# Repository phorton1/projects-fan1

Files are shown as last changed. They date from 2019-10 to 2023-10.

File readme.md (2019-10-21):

## 3D PRINTED FAN with Brushless Motor

I live on a sailboat in the tropics.  A good working 12V fan is more than a luxury, it is a necessity.  They get used for 8, 12, or more hours per day, and apart from just the sheer wear and tear from so much use, they are also usually subject to high humidity and salty sea air.  I have 7 such fans on the boat (it's a big boat, with 3 cabins).   One in each of the guest cabins, two in the master cabin, two in the salon, and one over the stove that works as an exit fan to a nearby window. So, if the fans only last 6 months ... well, you can see that you will be replacing a lot of fans!

For over 10 years I have struggled to get a good working 12V fan at anything resembling a reasonable price.

Such fans for boats (and RVs) come in basically two genres:

* super cheap fans, that aren't even worth the effort
* expensive boutique fans that don't satisfy expectations

Basically you can get cheap fans with brushed motors and cheap steel or plastic housings, or expensive ones that don't seem to me to be worth the money. If you are interested in more details, here's a link to my "survey of existing fans" page: [Survey of Existing Fans](survey.md) where I cover mostly the "cons" of such fans.

But now that I have a 3d printer I was able to design **my own fan**, and I think it came out pretty good!

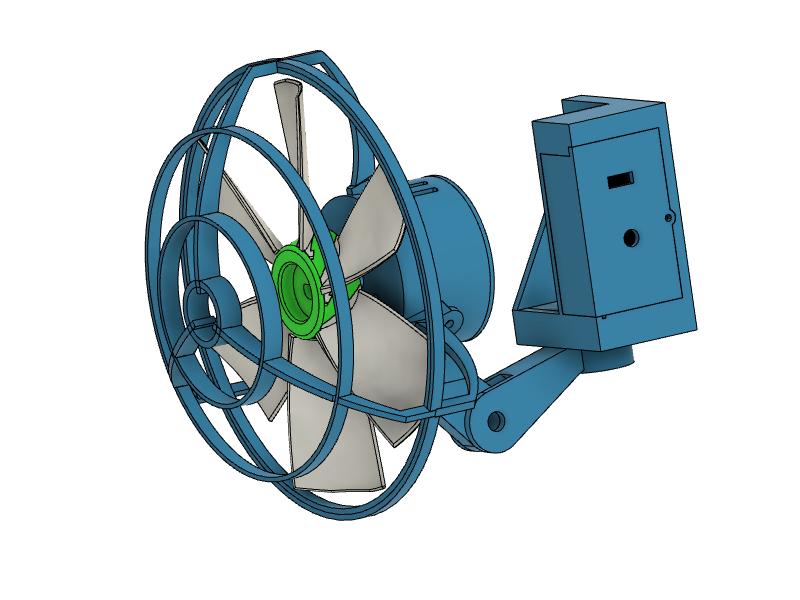
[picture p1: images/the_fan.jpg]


## MY SOLUTION

I went on ebay and bought a good brushless motor with dual ball bearings for $12.74.  To that I added a $3 arduino nano (which was really overkill for the project), a $1 rotary controller, a 50 cent switch, a little circuit board, and some wire, and designed and printed this fan.

The motor I chose was a Nidec 48F704K.   It seemed to have about the right specs for rpms and amperage at 12V.  They are actually a bit big for the fan I designed.  My fan has 180mm/7" blades and this motor could easily push 9" blades, but I wanted one that fit basically with the footprint of the "standard" fan I am replacing (which has 6" blades).

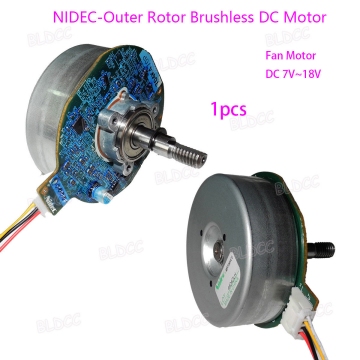
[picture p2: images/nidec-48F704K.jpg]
  **$12.74 on ebay**

**The motor takes short 3mm screws.**

I went through several design iterations, first on the fan blade, and then also on the shroud. Here's a pic of an early prototype.  Notice the bench power supply to the left, the laptop with fusion360 running and my Prusa 3d printer in the background.  With this setup I was able to test the fan at various voltages and to monitor and measure the current consumption:

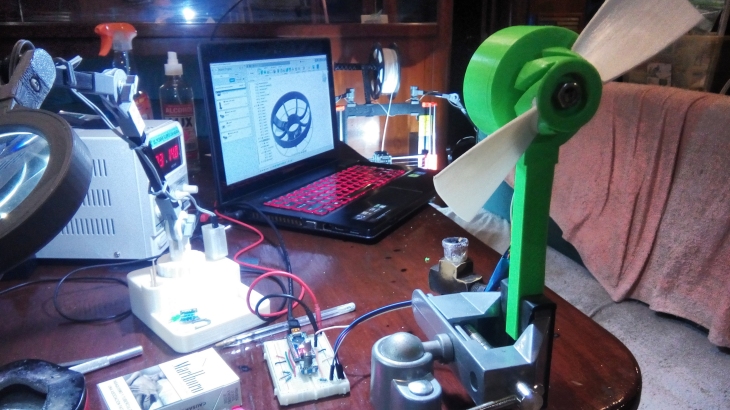
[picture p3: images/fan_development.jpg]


I was surprised at how much (negative) effect the shroud had on the performance.   I started with a heavy shroud that printed in one piece.  It took 11 hours to print, with supports!   That was for the birds!   I redesigned it  to be much thinner and less obtrusive to the airflow, and so that it could be printed in an hour or two, though it needs assembly. 

I had already (quickly) learned that it was better to print the blade itself in pieces and assemble it.   Printing it in one piece took a long time (like 8-10 hours), and (b) did not allow for replacing a single blade should one break.

Let me also add that this is **NOT THE FINAL effort** in this matter!  I have purchased more additional, and different types of brushless motors on Ebay and am looking forward to refining and generalizing the mounting etc.

## SLICING and PRINTING

All the STL files are in the [STL subdirectory](stl/).  I have provided the [Fusion 360 files](fusion/) as well.

I print almost everything at **0.30mm layer heights**, in "draft" quality on the Prusa, except the blades, which I printed at the Prusa 0.20mm "quality" setting.

I try to orient all the parts so that they are strongest in the required directions.  For the blade, to minimize the amount of supports, I print them on edge, as shown below:

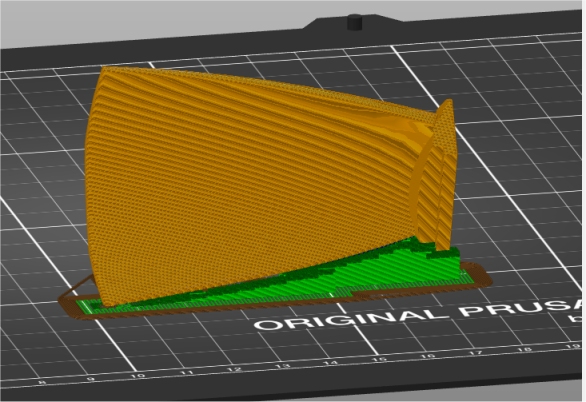
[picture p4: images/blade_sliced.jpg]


I print all the rings for the shroud in one go, with the slots facing upwards as shown below.

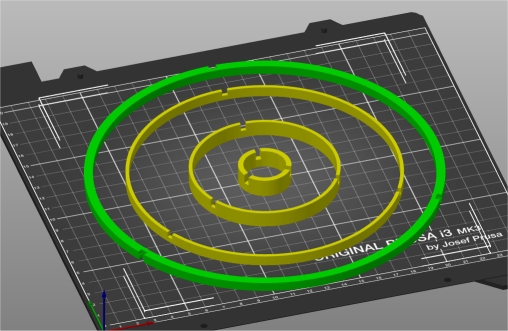
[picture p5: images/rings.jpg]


and the motor body, with supports, as shown below:

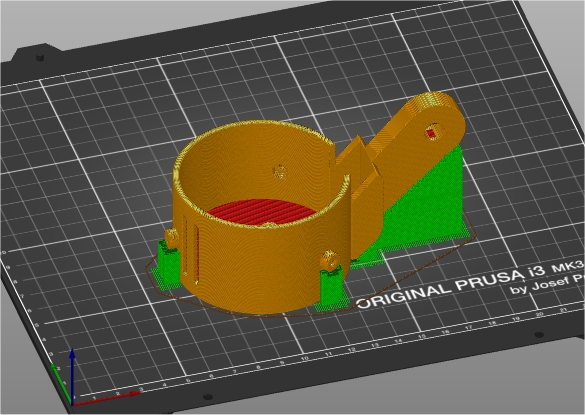
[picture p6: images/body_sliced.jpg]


The rest of the parts (bracket, struts, etc) are generally printed laying flat, or in whichever orientation makes the most sense.

## The Circuit

For the PWM motor control circuit, I simply used an Arduino Nano.  This was nice because I could hook it up directly to the boat's 12V system (which actually varies from about 12V upto 14.00V while charging) and it in turn could provide 5V that I could use with the rotary controller and for the PWM control signal to the motor.   Even so, it is overkill, so future designs will probably be based on the AT-TINY13 8 pin MPU with a dedicated 12V regulator, which sounds complicated but is actually less expensive ($1 vs $3) compared to the arduino and physically much smaller.

I already had pins on the nano, so I just soldered a few of them to the underlying circuit board.   

This is a common circuit available elsewhere on the net ... and I don't feel like redrawing it!  It is basically used as the cannonical example of how to hook up a rotary controller to the arduino.  Instead of powering an LED, I just attach it to the PWM inputs to the motor instead:

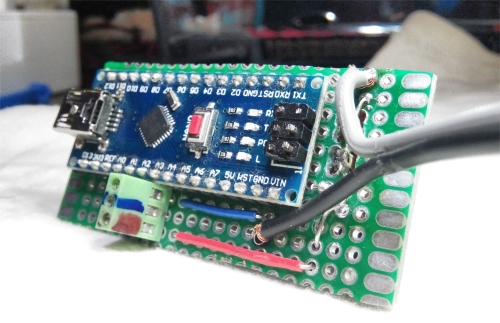
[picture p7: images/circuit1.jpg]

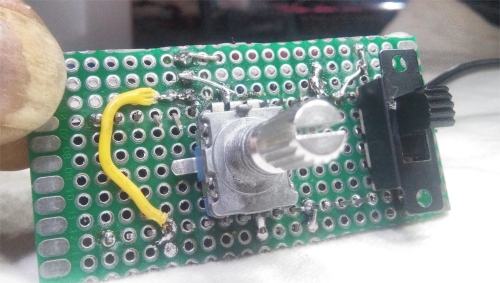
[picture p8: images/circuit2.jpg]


Note that there are no additional components (resistors) on the circit.  I take advantage of the built in pull-up resistors on the nano and just connect the rotary controller and fan directly to nano pins!

By the way ... the on-off switch completely cuts of power to the fan and nano ... it is not a "software" switch.  The fan draws **no power** when it is not turned on.

Finally, the Arduino sketch I am using is available [here](ino/).  In the future I will probably forgo the rotary control and save 50 cents and just use a 5K pot with a voltage divider ....

## Summary

I have mounted the fan in the master cabin.  I use it every night, all night long. It is quiet, it hums nicely, and puts out volumnous amounts of air.   It is using about 0.7 amps ... slightly less than half the power of the cheap "standard" fan, and puts out about twice as much air.  I will check back in a year and see how it is handling the wear and tear.

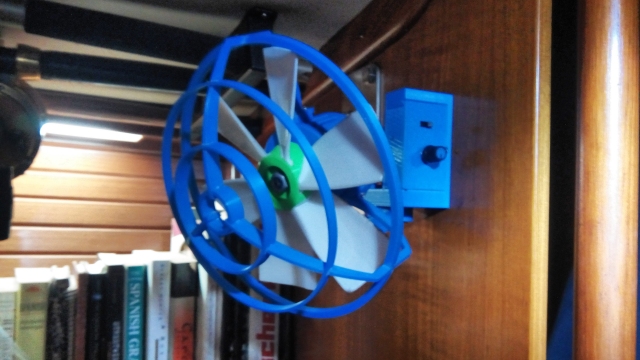
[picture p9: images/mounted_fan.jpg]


I'm calling this a **SUCCESS!**

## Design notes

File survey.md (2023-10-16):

# Survey of existing fans

## Not Recommended

 Here are pics of some I definitely don't recommend.  All of these use brushed motors which have a maximum lifetime of about 6 months under heavy use.  They vary in price from about $15 to $50, and are always the same, regardless of the price you pay.

They used to make the first kind below with just an on/off switch, which was better, but in any case, the bracket is very cheap, and it rusts, and now, with the separate control box, you have to mount TWO things every time you have to change one of these cheap fans.  I hate em!

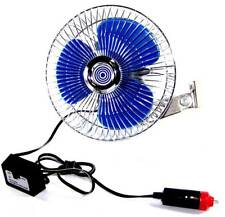
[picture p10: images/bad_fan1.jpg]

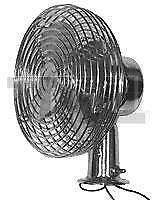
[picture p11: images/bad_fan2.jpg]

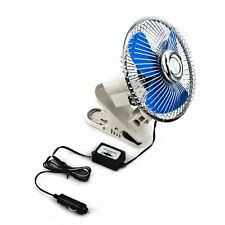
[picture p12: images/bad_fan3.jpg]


The second one, with a chromed mild steel housing and aluminum blades rust and make a lot of noise.  They typically come with a 2 speed controller that usually fails after about 2 months.  The blades are terribly inefficient and the controllers get VERY hot.  In fact, one of them almost caught on fire once on the boat.  I woke up to the smell of ozone and a black mark was burned into the headliner of the boat when the fan failed. I have one now (probably the fourth of these I've had) that barely works and will soon be replaced with a 3d printed (or other*) fan.  You can get this fan for $20, or you can pay $47 for the same fan. Doesn't matter.

The last one has no permanent mounting bracket, and is just a variant of the 1st one.

## The "standard fan" I ended up using

So, over the years, I had "standardized" down to a fan that looks like this:

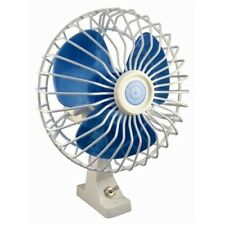
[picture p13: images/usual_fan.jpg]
 **The "Standard" fan I have been using**

These fans have a vinyl coated mild steel shroud, and a plastic case with a oscilatting mechanism and a power switch.  They can be had from $25 upto about $60.  Same fan. $60 from West Marine, $25 on ebay.  The oscilating mechanism itself makes a lot of noise, as well as causing it to jam at times, and so usually I end up disassembling the fan and removing it. The brushes last between 6 months and year at most, but before they completely wear out you will have usually disassembled and re-assembled the fan at least once to clean the insides, which get covered with carbon dust, and to correct the alignment of the brushes, which, due to the design, tend to wear in such a way that they jam when they are about 1/2 worn out.

These fans move a reasonable amount of air, and use between 1 and 1.6 amps at 12V ...

## Expensive "boutique fans"

Here's some pics of some of the other commonly available "boutique" fans for boats.  Notice the hefty prices:

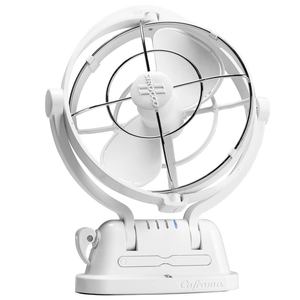
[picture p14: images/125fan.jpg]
  **$125 !!!**
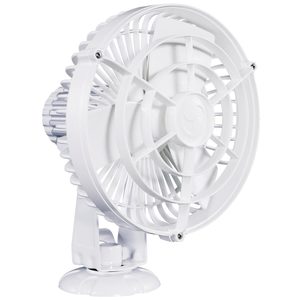
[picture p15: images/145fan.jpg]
  **$145 !!!**
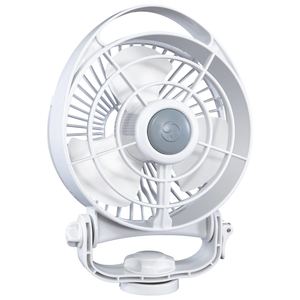
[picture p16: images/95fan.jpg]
  **$95 !!!**

I have never been able to justify shelling out that kind of money for a small 12V fan.  They are more expensive mostly. I think, because they use brushless motors and because they are marketted specifically to boaters.  Add "boat" to the description of an item and it costs twice as much!  I'm not kidding ... I've seen the exact same alternator for a motor sold for $50 for cars, and $125 for boats!  In regards to fans, I'm pretty sure these fans are better than the cheap ones, but I don't think they are worth the amount being charged.

## Endless Breeze

Finally, for completeness, there is one fan that I DO sort of recommend, if you have room on the boat for it, and are willing to spend $120+ for a fan.  That is the "Endless Breeze" 12V fan from dometic.   I have seen them on ebay from about $110 to $160:

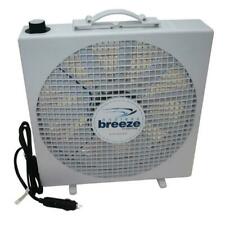
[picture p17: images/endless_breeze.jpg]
  **$110+**

This fan is big, about 15"x15"x4" and is not really appropriate for mounting on a wall above a berth or in a small cabin, but it works well, is quiet, and seems like it will last forever, so it *may* be appropriate for a boat.   Definetely handy to have.

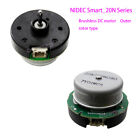
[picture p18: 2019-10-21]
images/nidec_20N.jpg

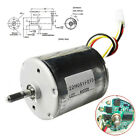
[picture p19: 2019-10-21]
images/nidec22H051F.jpg

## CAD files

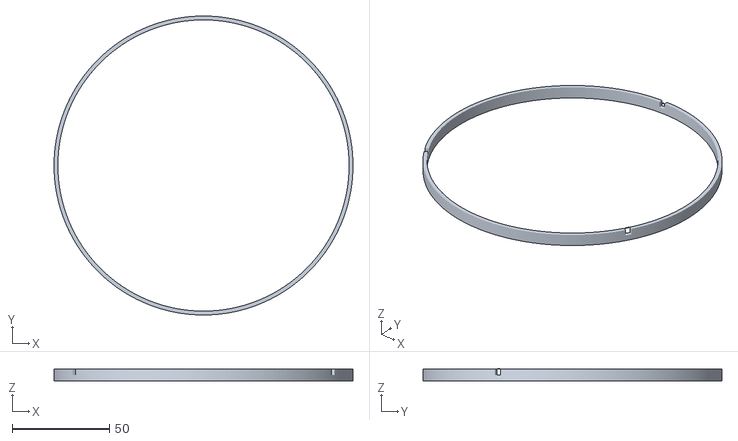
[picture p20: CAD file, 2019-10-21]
stl/ring2.stl
154.0 x 154.0 x 6.26

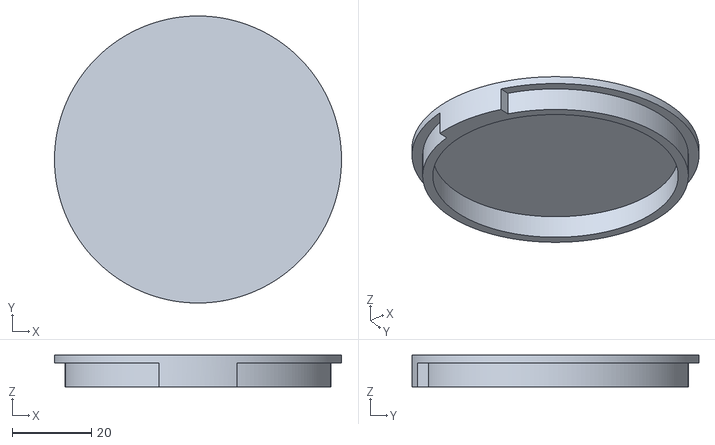
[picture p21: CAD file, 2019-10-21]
stl/back_plate.stl
72.5 x 72.5 x 8.00

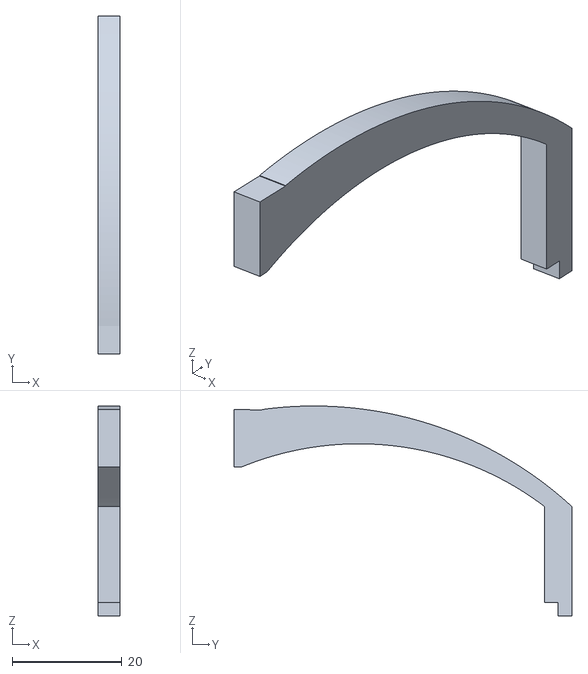
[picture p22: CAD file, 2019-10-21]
stl/back_strut_part1.stl
4.00 x 61.6 x 38.3

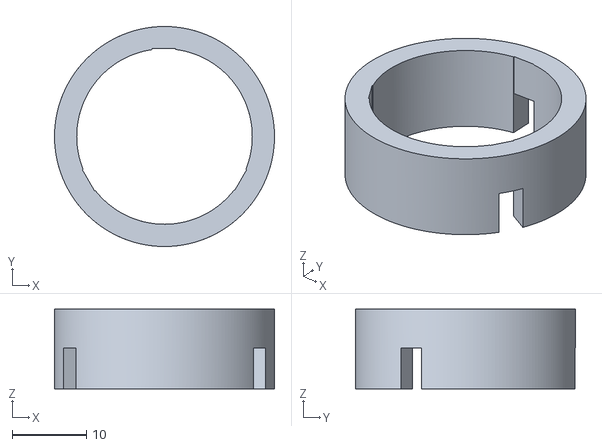
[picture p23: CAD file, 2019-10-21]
stl/ring4.stl
29.6 x 29.6 x 10.7

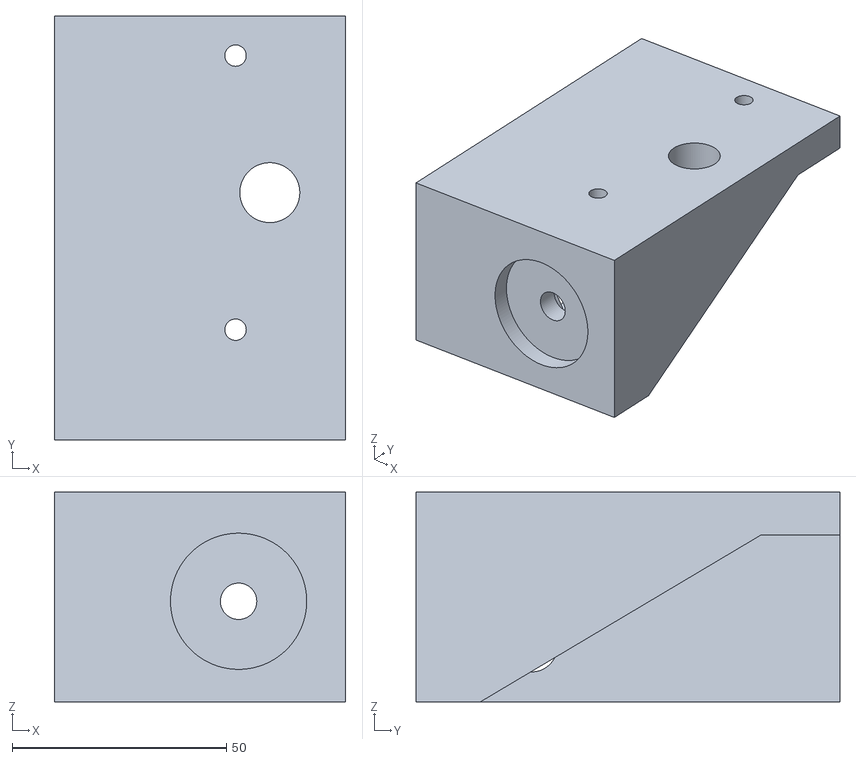
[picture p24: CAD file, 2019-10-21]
stl/wall_bracket.stl
68.0 x 99.0 x 49.0

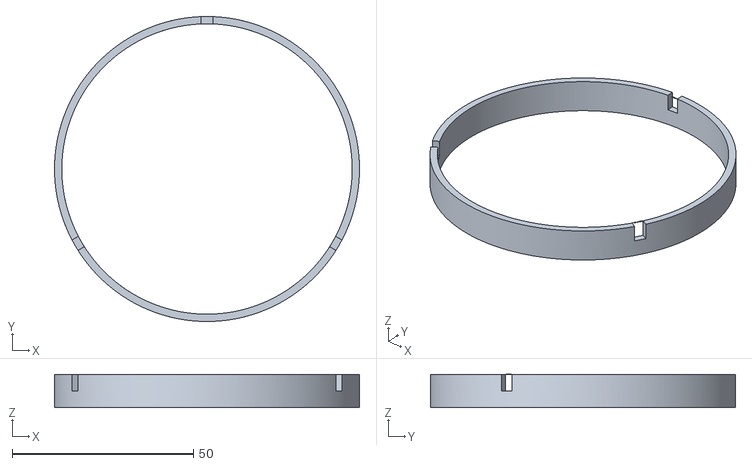
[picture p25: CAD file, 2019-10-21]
stl/ring3.stl
84.0 x 84.0 x 9.21

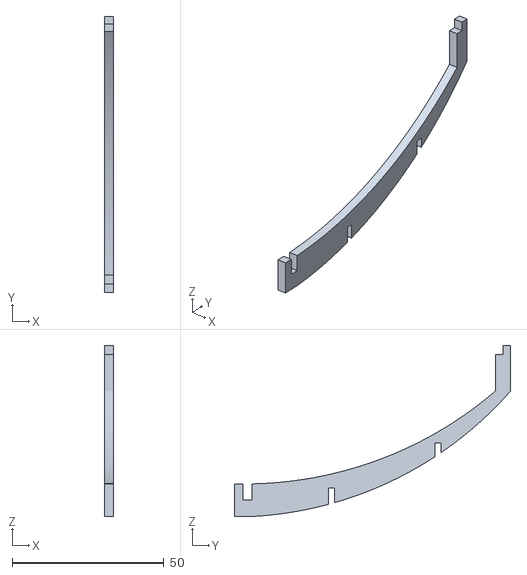
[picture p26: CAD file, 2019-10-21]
stl/front_strut.stl
3.00 x 91.0 x 56.4

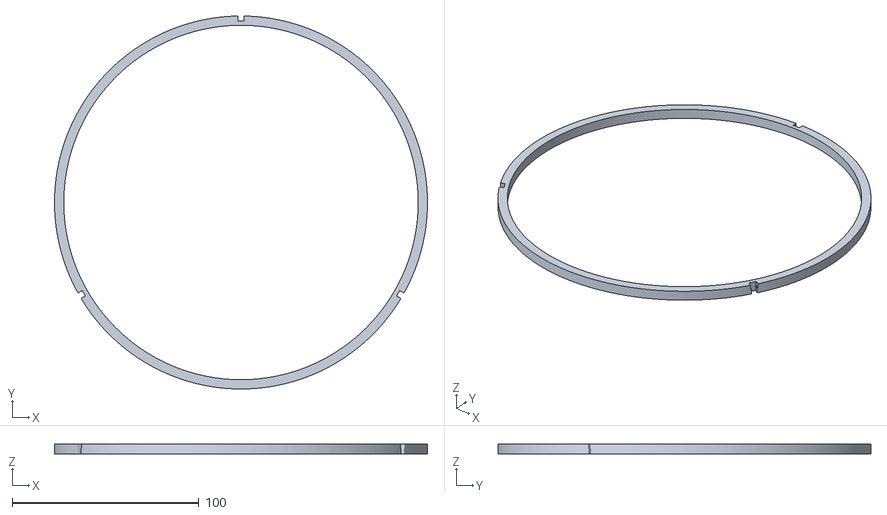
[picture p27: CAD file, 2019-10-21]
stl/ring1.stl
200.0 x 200.0 x 5.50

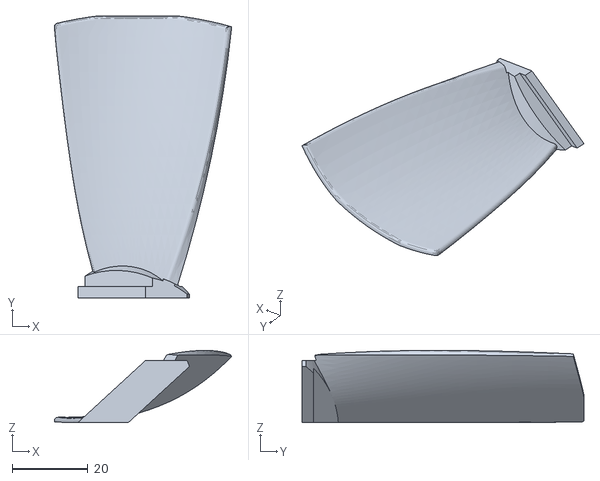
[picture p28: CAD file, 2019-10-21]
stl/blade3.stl
46.8 x 74.4 x 19.0

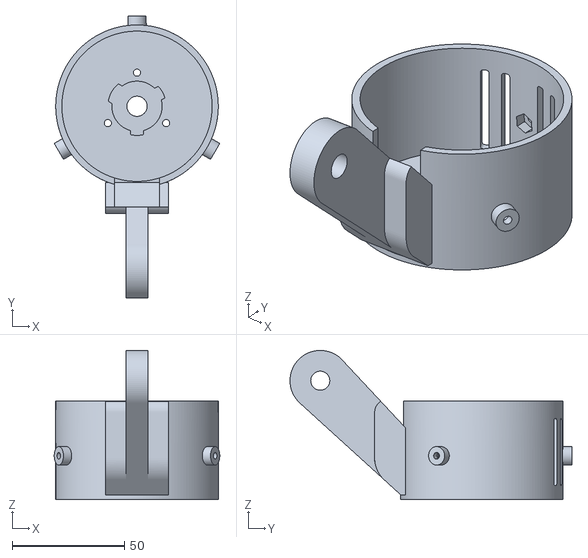
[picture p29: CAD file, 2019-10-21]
stl/motor_body.stl
73.8 x 125.7 x 66.5

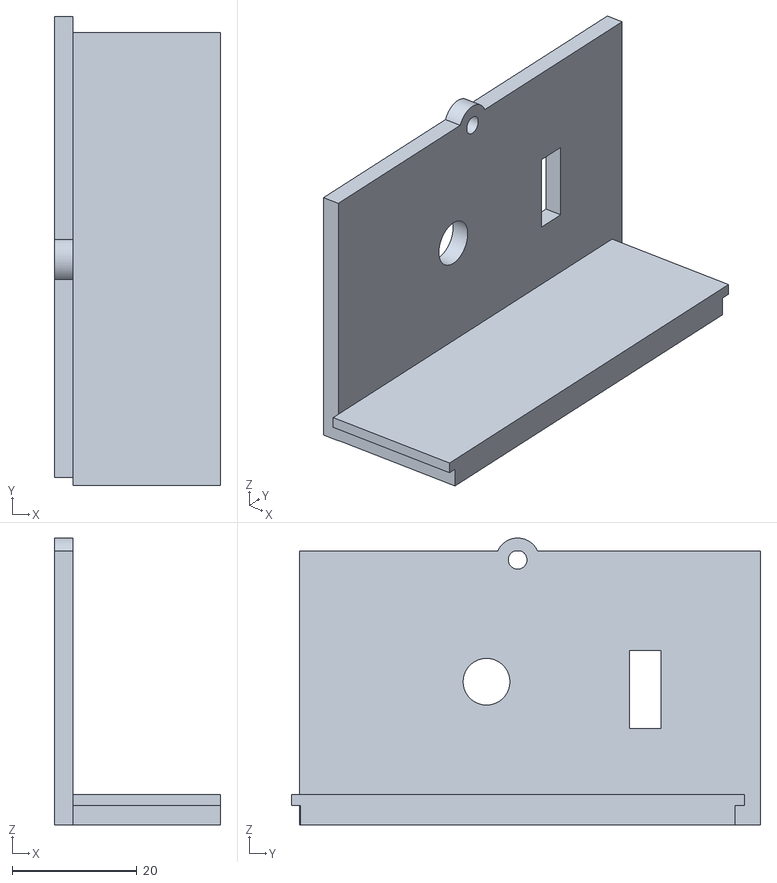
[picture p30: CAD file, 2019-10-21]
stl/box_cover.stl
26.7 x 75.3 x 46.1

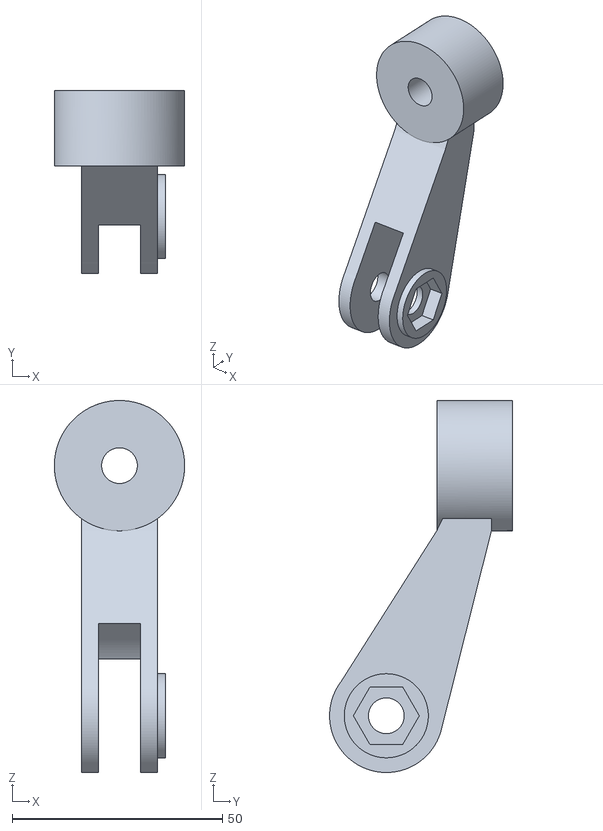
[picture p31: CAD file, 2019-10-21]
stl/bracket.stl
31.0 x 43.5 x 88.5

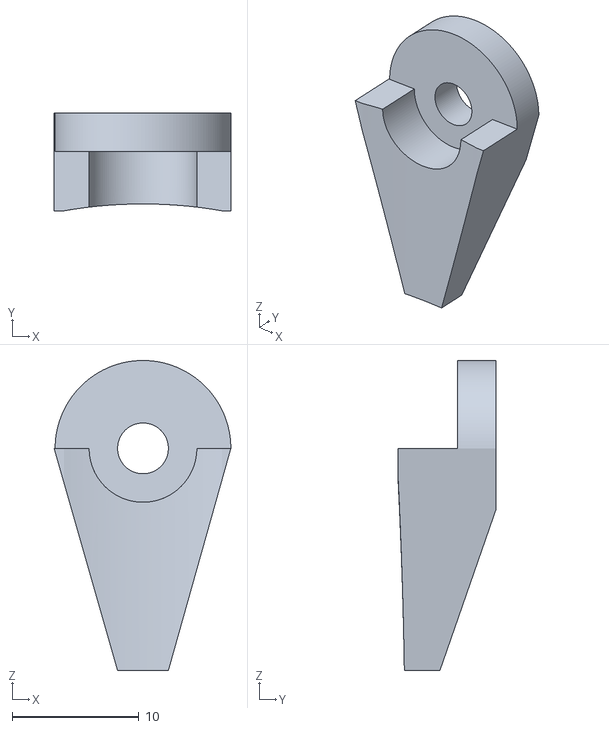
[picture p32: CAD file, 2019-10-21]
stl/back_strut_part2.stl
13.9 x 7.69 x 24.4

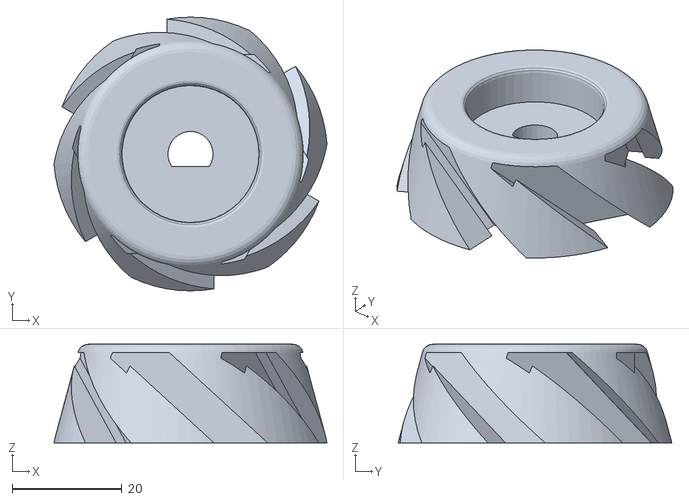
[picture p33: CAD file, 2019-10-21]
stl/hub3.stl
49.9 x 50.0 x 18.0

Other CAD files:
fusion/fan1.f3d

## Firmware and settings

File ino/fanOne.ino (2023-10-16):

// UI:
//
//  The fan remembers the last setting.
//  It waits 10 seconds before writing EEPROM to save writes.
//  Boot with button pressed resets level to 0 and stores it.
//
//  The fan stops at 90% duty cycle
//  The fan is at it's max at 10% duty cycle (or grounded)
//  The fan level is from 0..79, representing duty cycles
//      from 100/90% down to 10/0%.  Each rotary encoder detent
//      the value by 4 (so there are twenty steps)


#include <EEPROM.h>
// #include "myDebug.h"

#define MAX_FAN_LEVEL       79
#define FAN_LEVEL_INC       4

#define PIN_ENCODER_A       A3      // rotary encoder input pin
#define PIN_ENCODER_B       A5      // rotary encoder input pin
#define PIN_BUTTON          6       // rotary encoder button pin
#define PIN_PWM_OUT         9       // pwm out to fan
#define EPROM_ADDR          2

#define FAN_LEVEL_WRITE_TIME  5000 // milliseconds

int fan_level = 0;
int fan_level_change_time = 0;


int readEncoder()
{
    int inc = 0;
    static unsigned char last_encoder_A = 0;
    unsigned char encoder_A = digitalRead(PIN_ENCODER_A);
    unsigned char encoder_B = digitalRead(PIN_ENCODER_B);

    if (!encoder_A && last_encoder_A)
    {
        if (encoder_B)      // B is high so clockwise
            inc = FAN_LEVEL_INC;
        else                // B is low so counter-clockwise
            inc = -FAN_LEVEL_INC;
    }
    last_encoder_A = encoder_A;  // Store value of A for next time
    return inc;
}


void setFanLevel(int level)
{
    float pct = ((float)(MAX_FAN_LEVEL-level)) / MAX_FAN_LEVEL;
    int pwm_value = pct * 255.0;
    if (pwm_value < 7) pwm_value = 7;
    // display(0,"  pwm_value=%d",pwm_value);
    analogWrite(PIN_PWM_OUT, pwm_value);

}


void storeFanLevel(int level)
{
    // display(0,"storing=%d",level);
    EEPROM.write(EPROM_ADDR,level);
}


int recallFanLevel()
{
    int level = EEPROM.read(EPROM_ADDR);
    // display(0,"recalled=%d",level);
    if (level < 0 || level > MAX_FAN_LEVEL)
        level = 0;
    return level;
}



void setup()
{
    // Serial.begin(115200);
    // delay(1000);
    // display(0,"fanTest.ino started",0);

    pinMode(13,OUTPUT);
    pinMode(PIN_PWM_OUT, OUTPUT);
    pinMode(PIN_ENCODER_A, INPUT_PULLUP);
    pinMode(PIN_ENCODER_B, INPUT_PULLUP);
    pinMode(PIN_BUTTON, INPUT_PULLUP);

    if (!digitalRead(PIN_BUTTON))
    {
        fan_level = 0;
        // display(0,"RESET",0);
        storeFanLevel(fan_level);
        for (int i=0; i<21; i++)
        {
            digitalWrite(13,i&1);
            delay(100);
        }
        while (!digitalRead(PIN_BUTTON));
    }
    else
        fan_level = recallFanLevel();

    setFanLevel(fan_level);
}



void loop()
{
    uint32_t now = millis();
    static uint32_t last_time = 0;
    if (now > last_time)    // every ms
    {
        last_time = now;
        int inc = readEncoder();
        int level = fan_level + inc;
        if (level < 0)
            level = 0;
        if (level > MAX_FAN_LEVEL)
            level = MAX_FAN_LEVEL;
        if (level != fan_level)
        {
            // display(0,"fan_level = %d",level);
            fan_level = level;
            setFanLevel(fan_level);
            fan_level_change_time = millis();
        }
        else if (fan_level_change_time &&
            (now > fan_level_change_time + FAN_LEVEL_WRITE_TIME))
        {
            fan_level_change_time = 0;
            storeFanLevel(fan_level);
            for (int i=0; i<17; i++)
            {
                digitalWrite(13,i&1);
                delay(100);
            }
        }
    }
}
